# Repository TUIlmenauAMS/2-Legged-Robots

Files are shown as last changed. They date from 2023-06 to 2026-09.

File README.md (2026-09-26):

# 2-Legged-Robots

Program and 3D printing parts and description for little 2-legged robots, like in this picture,
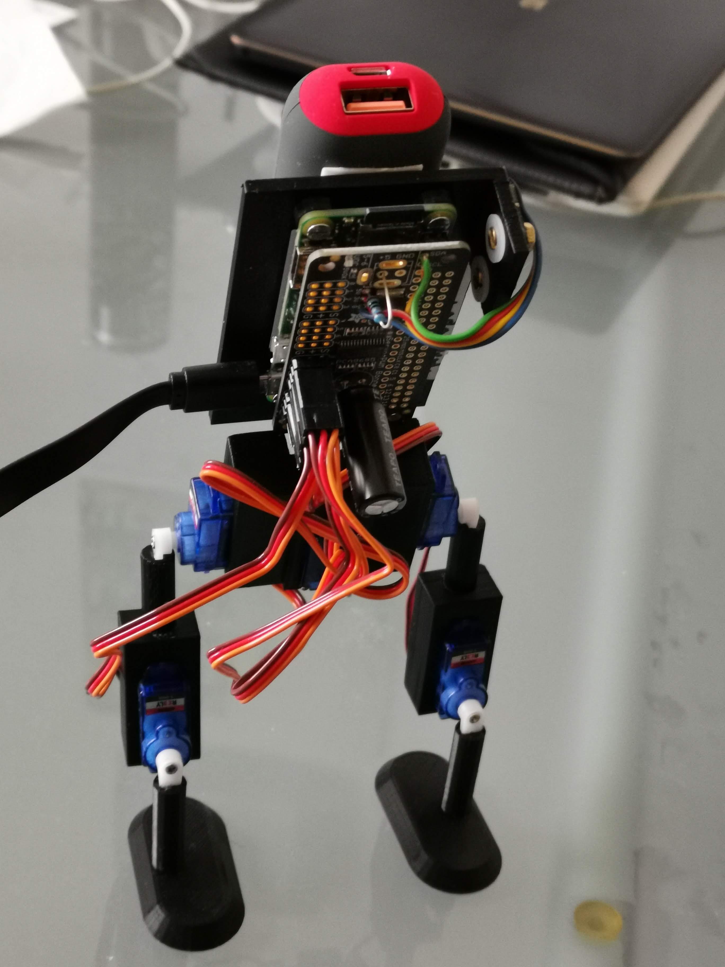
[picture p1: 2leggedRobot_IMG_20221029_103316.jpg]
.

Here is a video of the robot in action. There you can see the sideways spine joint and servo from behind (the white latch). This enables a simple and efficient way to shift the center of mass from one foot to the other, for walking:

https://player.vimeo.com/video/791830780?h=ef3d78c103

The "stl" parts are for my Raspirobo7 robot.
The "..bin.stl" files are binary stl files, which are needed for a MuJoCo simulation.
(Here is a partial simulation for back and hip: https://colab.research.google.com/drive/190HttyWH3-cmfSE2mszep3_cSGHyP7G-?usp=sharing)

Here is a complete simulation of the somewhat creative robot that was generated by Grok Build from this repository, which sill shows the resulting walking motion from the interplay of physics and the Python program, with a nice user interface for trying it out. You can also drag the view:

https://earth-drift-prairie-falcon.grok.me/

Building the robot needs:

- 2 foot_round075.stl

- 1 hueftservos.stl

- 2 knieservo_scad.stl

- 1 ruecken2.stl

Further parts:

- It is controlled by a Raspberry Pi Zero WH.

- Terratec P1 Powerbank Li-Ion 2600 mAh 171649, 5.49eur

- 5 servo motors REELY 36 ANALOG- SERVO 0008
(Nr. 1365555 / 4016138986273 or successor 2148502) at 4.99 eur (each)

- 3 AXIS DIGITAL ACCELERATION SENSOR MO, e.g. MMA8452Q
650514 / 4053199509867 , 6.99 eur.
Alternative MAKERFACTORY MF-6402108 accelerometer 
https://www.conrad.de/de/p/makerfactory-mf-6402108-beschleunigungssensor-1-st-2134036.html
7.49 eur.

- Elektrolytic-Capacitor 2200 uF, 16V,
Nr.: 1328835 - 62
Conrad Nr.: KSE228M016S1GBH25KFT, 0.20 eur

- 1 or 2 Ohm resistor 

- 4 wires, blue, yello, red, green.

- Ada3416  Adafruit 16-channel PWM/Servo.. 10.25
https://shop.pimoroni.com/products/adafruit-16-channel-pwm-servo-bonnet-for-raspberry-pi?variant=2821150736394 

- Micro SD Card, 32 GB, Noobs, 9.73 eur
https://shop.pimoroni.com/products/noobs-32gb-microsd-card-3-1?variant=31703694245971

The 2 ohm resistor is for the low pass filtered power suppy of the servo board. Since the servos can draw high power peaks, the 2200 uF capacitor is needed to supply thos power peaks. The resistor limits the current from the battery, to keep its volatge stable, to avoid the raspberry pi rebooting from a voltage drop. The 2 ohm resistor is solered in the servo board from the upper 5V soldering hole (viewed from looking at the front of the robot) to the left round soldering hole of the (unused) power plug. 

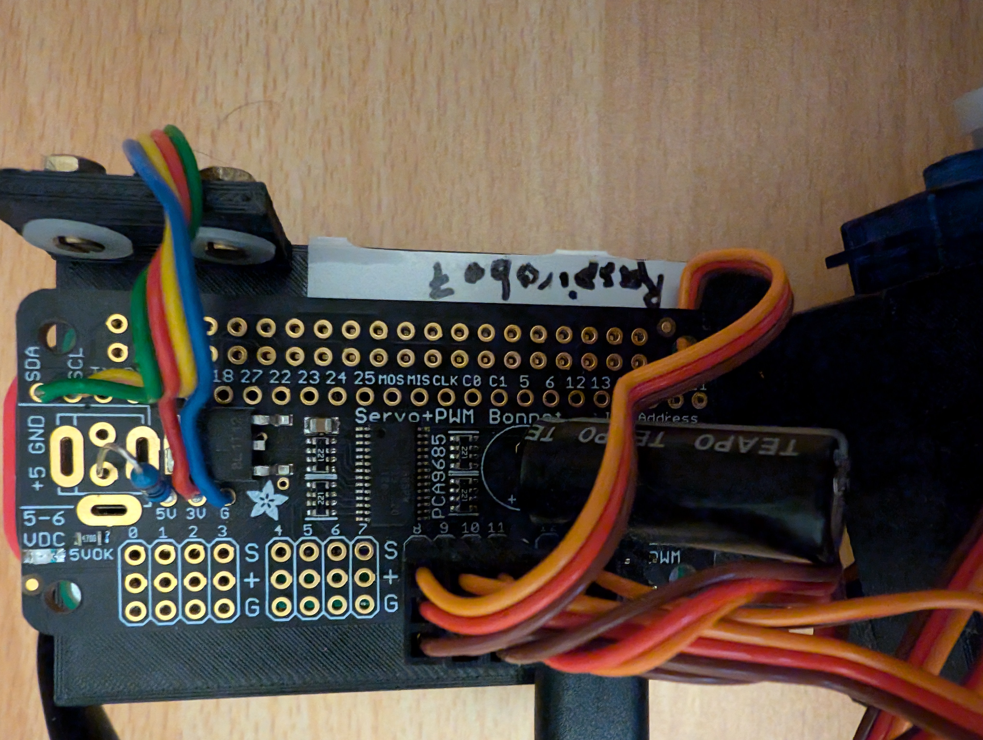
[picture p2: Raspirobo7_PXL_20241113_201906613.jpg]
This can be seen in this picture .

The acceleration sensor has the connections GND, scl, sda, 3V. They need to be connected, using flexible wires and soldering, to the corresponding soldering holes on the upper part ot the servo board.

As a first test after completing the hardware: after connecting with power, the LED's of both, the raspberry pi zero and also the servo shield, should light up. If not, the power is missing there.

The program "raspirobo7servoset90_only.py" sets all servos to the 90 degree position, for adjusting the legs and back to be straight at that position. This can also be used for testing the servos.

The program "raspirobo7servosetVertTilt.py" is for testing the accelerometer and find a vertical tilt angle that lets the robot stand in rest. This angel is then to be entered in the walking program "raspirobo7_balancing_learning2.py".

The program to let the robot walk in a learning manner is: "raspirobo7_balancing_learning2.py"

It uses our probabilistc optimization of "Random Directions" for learning and optimizing the walk. Hence it might take a while in the beginning until it learns to balance and walk.

Also see the information and videos on our Robotics website:

https://www.tu-ilmenau.de/en/university/departments/department-of-electrical-engineering-and-information-technology/profile/institutes-and-groups/applied-media-syste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

Many greetings,

  Gerald Schuller

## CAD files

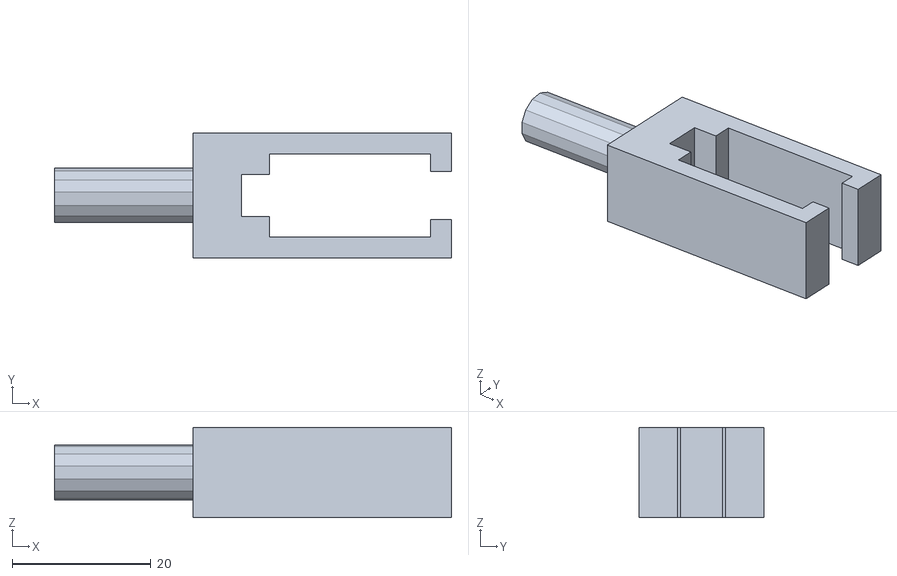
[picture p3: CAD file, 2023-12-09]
knieservo_scad-bin.stl
57.3 x 18.0 x 13.0

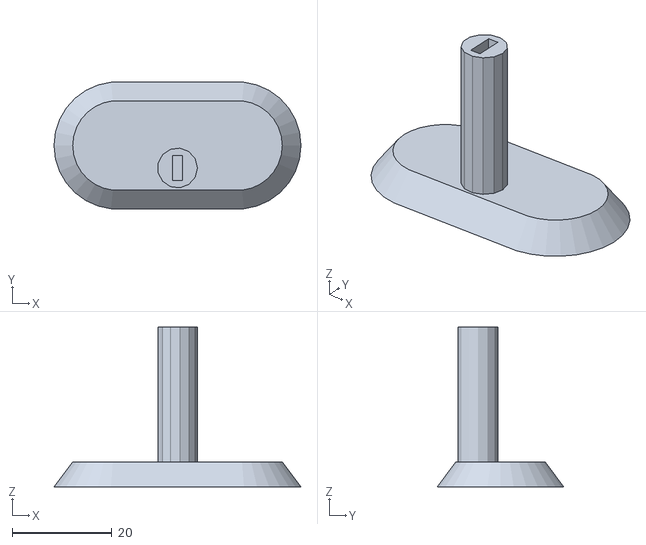
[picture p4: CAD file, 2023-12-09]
foot_round075-bin.stl
49.5 x 25.4 x 32.0

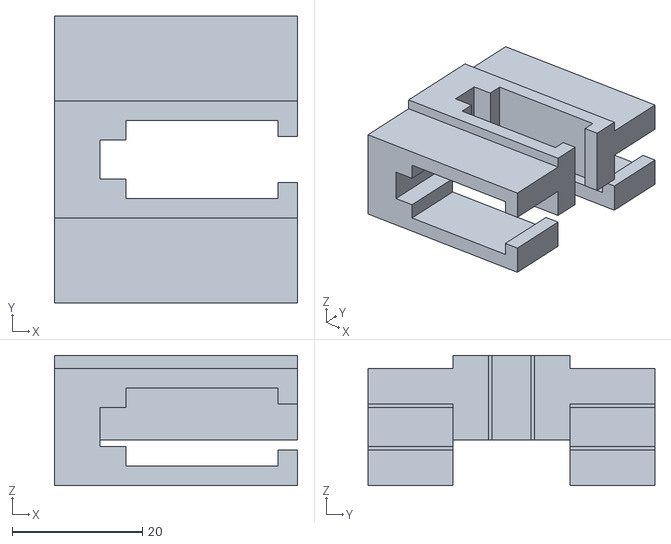
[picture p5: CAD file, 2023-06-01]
hueftservos_bin.stl
37.3 x 44.0 x 20.0

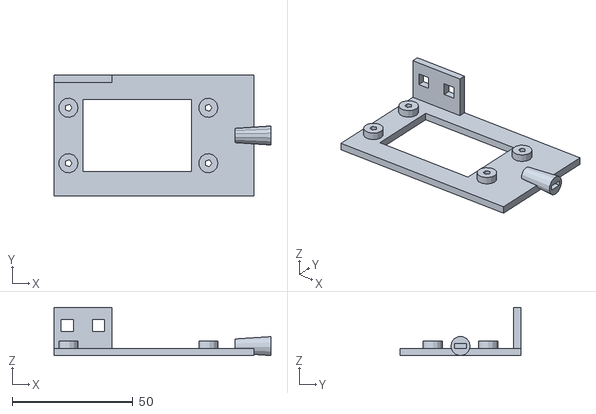
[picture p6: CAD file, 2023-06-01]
ruecken2bin.stl
90.0 x 50.0 x 20.0

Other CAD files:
hueftservos.stl
foot_round075.stl
ruecken2.stl
knieservo_scad.stl

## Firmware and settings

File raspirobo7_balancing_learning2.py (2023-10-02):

#Program to test the Raspirobo7 Robot with accelerometer and servo movement.
#For learning to balance itself using the random directions optimization.
#With side learning and storing of the optimized coefficients.
#Seems to be too wild after a while.
#Optimize for minimum variation for accelerometer measures despite disturbances from knee movements.
#Run it with:
#python3 raspirobo7_balancing_learning2.py
#
#You can check the I2C addresses of the devices connected to the Raspberry Pi using:
#sudo i2cdetect -y 1
#
#Includes a
#function to read accelerometer sensor MMA8452Q from the Raspberry Pi I2C port.
#See: http://ozzmaker.com/guide-to-interfacing-a-gyro-and-accelerometer-with-a-raspberry-pi/
#Based on:
#https://github.com/ControlEverythingCommunity/MMA8452Q/blob/master/Python/MMA8452Q.py
#Connections:
#http://www.pibits.net/code/mma8452q-accelerometer-and-raspberry-pi-example.php
#
#Data Sheet of MMA8452Q:
#https://www.robotshop.com/media/files/pdf/triple-axis-accelerometer-breakout-board-mma8452q-headers-datasheet.pdf
#Activate I2C bus on Raspi with "sudo raspi-config"
#Then:
#sudo apt-get install build-essential libi2c-dev i2c-tools python-dev libffi-dev
#sudo pip install cffi smbus2 (for python2, for python3 it should be smbus and pip3)
#sudo pip3 install adafruit-circuitpython-servokit
#name: raspirobo7
#Gerald Schuller, November 2022

#import smbus2 as smbus #for Python2
import smbus   #for Python3, install with pip
from lsm303d import LSM303D #install with pip
import time
import numpy as np
#from scipy.signal import medfilt
#import optimrandomdir as opt
import optimrandomdir_timevarying as opt

# Get I2C bus
bus = smbus.SMBus(1)
#For the servos:
from adafruit_servokit import ServoKit
lsm = LSM303D(0x1d)  # Change to 0x1e if you have soldered the address jumper


def readaccelerometer():
   #Read current accelerometer values
   #returns:
   #List of 3 float acceleration-values, [x,y,z]
   xyz = lsm.accelerometer()
   
   return xyz

#def balancing_obj(kcoeffs, tilts): #optimizing only side balance
#def balancing_obj(kfcoeffs, tilts): #optimizing only forward balance
def balancing_obj(coeffs, tilts):  #optimiizing both, side and forward balance
   #Objective function for balancing the robot such that the accelerometer is aligned to verttilt and hortilt, 
   #which are the sin of the angles to the vertical axis, vertical (front/back) and horizontally (left/right).
   #Arguments: kcoeffs: coefficients for the control lop
   #tilts: (verttilt, hortilt) target directions for balancing
   #Returns the error or objective function to minimize
   
   global YLP, YLPold, ydist, yold, Yvar, ZLP, ZLP1, ZLPold, ZLP1old, zdist, zold, Z, Zvar, phase, ampRH, ampLH;
   
   (verttilt, hortilt) = tilts  #hortilt is optimized
   kcoeffs=coeffs[0,:]
   kfcoeffs=coeffs[1,:]
   #hortilt=kcoeffs[3] #learned horizontal tilt
   #verttilt=kfcoeffs[3] #learned forward tilt
   
   for balancetrials in range(100): #Number of iterations for a set of control coefficients from optimizer, 
      #objective functions is returned at the end, to have a clearer picture if it is good.
      (X,Y,Z)=readaccelerometer()
      X=-X; Z=-Z #sign change for rotated accelerometer
      #print("(X,Y,Z)=", (X,Y,Z))
      #Y's:
      ydist+= (Y-verttilt)*(timestep);        #integral values (distance traveled, without artificial factor 100)
      ydist=np.clip(ydist,-0.1,0.1);
      YLPold=YLP
      YLP=0.99*YLP+0.01*Y
      yspeed=(Y-yold)/(timestep);  #differential values (speed, without artificial factor 100)
      ylpspeed=(YLP-YLPold)/(timestep)  #vert. speed from low passed version

      #Z's:
      """
      Zmem[0:(Lmed-1)]=Zmem[1:Lmed] #shift samples 
      Zmem[Lmed-1]=Z  #write latest sample, for median filter
      Z=medfilt(Zmem,kernel_size=Lmed)[int((Lmed-1)/2)]
      """
      
      zdist+= (Z-hortilt)*(timestep);
      zdist=np.clip(zdist,-0.1,0.1);

      #Sideways tilt:
      zspeed=(Z-zold)/(timestep);
      yold=Y;
      zold=Z;
      ZLPold=ZLP
      ZLP=0.99*ZLP+0.01*Z
      ZLP1old=ZLP1
      ZLP1=0.95*ZLP1+0.5*Z  
      zlpspeed=(ZLP-ZLPold)/(timestep)  #hor. speed from low passed version
      zlpspeed1=(ZLP1-ZLP1old)/(timestep) #hor. speed estimation from less low pass filtering
      
      #----------------------
      #PID control loop:
      #frontbalance = 180/3.14* 2.6*(ydist + 0.05*(Y-verttilt) -4*2.0e-2*ylpspeed) #2: schneller, without artificial factor 100
      #kf=np.array([1.3e+02, 6.3e+00, -1.2e+01, 5.6e-01]) #from learning robot 4, seems reasonably stable
      #kf=np.array([100, 100.0, -120])
      #kf=np.array([0, 6, 0])
      #kf=np.array([350, 20.0, -30])
      kf=kfcoeffs
      frontbalance = kf[0]*ydist + np.clip(kf[1]*(Y-verttilt),-10,10) + np.clip(kf[2]*ylpspeed,-10,10) 
      #sidebalance = -180/3.14* 2.9*(zdist + 0.05*(Z-hortilt) -2*4.0e-2*zlpspeed)*1.0;# k2=4e-4 #2: schneller, without artificial factor 100. k1 needs to be larger for faster steps, ca. 0.7 fuer speed 0.25. k2 was originally with - sign, but with plus seems to be better!
      #k=np.array([-3.2e+02, -1.5e+01, 3.4e+00, 1.4e-01]) #This set makes it oscillate! From learning robot4
      #Manual tuning of the PID controller: https://en.wikipedia.org/wiki/PID_controller
      #Increase each coeff until oscillation, then half it, first propoertional, then integral, then differential. 
      #k=np.array([-200, -1.5e+01, 28])
      #k=np.array([-350, -20.0, 30])
      #k=np.array([-1000, -1000.0, 1200]) #P: 30 makes it oscillate, so half: 15, I: 400 oscillates, so half, 200
      #k=np.array([-1000, -100.0, 10])
      #k=np.array([-1000, -100.0, 400])
      k=kcoeffs; #Read control coefficients from function argument
      #k=np.array([ 10.89118321,   4.93782397, -10.27297858,   3.8025568 ]); hortilt=k[3] #optimized with step excitation
      #k=np.array([ 10.89118321,   4.93782397, -10.27297858,   -0.15 ]); hortilt=k[3] #optimized with step excitation, k[3] needs to be manually tuned for back upright, more negative values tilt more left, as seen from the Robot. -0.3, -0.15. But attention: Changes because it is part of the optimization, which makes the robot sometimes turn or go in circles. So it could also be left at 0.0. Not really, kcoeffs is not used, only the preset above!
      sidebalance = k[0]*zdist + np.clip(k[1]*(Z-hortilt), -10, 10) + np.clip(k[2]*zlpspeed, -10,10) #+ np.clip(k[3]*zlpspeed1, -10,10)
      sidebalance=np.clip(sidebalance,-50,50);
      #print("sidebalance=", sidebalance)
      #print("k[0]*zdist=", k[0]*zdist, "k[1]*(Z-hortilt)=", k[1]*(Z-hortilt), "k[2]*zlpspeed=", k[2]*zlpspeed, "Z=", Z)
      #----------------------------
      #Servo control:
      angle=-frontbalance+110+1*ampRH; #sign change because of flipping hip servos, with tuning offsets. The number (110) needs to be manually tune for the legs being parallel in the beginning.
      huefterechts.angle=np.clip(int(angle + huefterechts_offset),0, 180); 
      angle=frontbalance+90+1*ampLH; #sign change because of flipping hip servos
      hueftelinks.angle=np.clip(int(angle + hueftelinks_offset),0,180); 
      #print("ampRK=", ampRK, "ampLK=", ampLK)
      
      #Independent Knee movements:
      #"""
      angle=0.4*sidebalance+knierechtsbalance+90-0-ampRK + knierechts_offset; #0.5
      knierechts.angle=np.clip(int(angle),0,180);
      #print("r=",np.clip(int(angle),0,180))
      angle=0.4*sidebalance+knielinksbalance+90+0-ampLK + knielinks_offset; #0.5
      knielinks.angle=np.clip(int(angle),0,180); 
      #print("l=",np.clip(int(angle),0,180))
      #"""
      
      #horangle=np.arcsin(hortilt)/3.14*180 #convert from radians to degrees
      #spine.angle = np.clip(int(90 + spine_offset - 0.0*horangle),0,180);
      #spine.angle = np.clip(int(90 + 0.6*sidebalance),0,180);
      spine.angle = np.clip(int(90 + 4.0*sidebalance),45,135); #2.0
      #spine.angle = 90 + spine_offset + hortiltdeg;
      #print("int(90 + spine_offset )=", int(90 + spine_offset ))
      #print("horangle=", horangle)
      #print("0.5*sidebalance=", 0.5*sidebalance)
      
      #Perturbation:
      #Move knees:
      """
      ctr+=1
      if ctr%50==0: #every second change horizontal tilt for control loop testing:
         hortiltoffset=-hortiltoffset
         #Perturbation at knees: Doesn't reall work because the balancing function overwrites it! Turned off the knee control
         angleknee=(np.random.rand()-0.5)*20 #+-5 Grad
         angleknee = -angleknee #flip direction
      """
      #Knee moves:
      """ 
      angleknee =-amptilt*np.sign(np.cos(phase))*(abs(np.cos(phase))**(0.5))
      #angleknee=(np.random.rand()-0.5)*20 #+-10 Grad
      #print("angleknee=", angleknee)
      knierechts.angle=90.0 + knierechts_offset+angleknee 
      knielinks.angle=90.0 + knielinks_offset + angleknee
      #walking movement back-forth:
      ampLH=-3.0*(np.sin(phase))
      ampRH=-3.0*(np.sin(phase))
      """
      #"""
      #Steps according to tilt:
      #hortiltoffset=-amptilt*np.cos(phase) #amptilt=-0.2,-0.08
      #angleknee=(np.random.rand()-0.5)*2 #+-1 Grad random excitation
      ampLH += np.sign(Z -hortiltadj)*5 #stepincrement
      ampLH= np.clip(ampLH, -5, 5)
      ampRH += np.sign(Z -hortiltadj)*5
      ampRH = np.clip(ampRH, -5, 5)
      #"""
      Yvar= 0.99*Yvar+0.01*((Y-YLP)**2)
      Zvar= 0.99*Zvar+0.01*((Z-ZLP)**2)
      phase+=speed
      time.sleep(timestep)
   print("Zvar=", Zvar, "Yvar=", Yvar, "Y=", Y)
   #print("kfcoeffs=", kfcoeffs)
   #print("fcoeffs=", coeffs)
   #return Zvar +Yvar
   #return Yvar
   #return Zvar
   return abs(Zvar-0.1) #0.06, 0.1, 0.15

#--------------------------------------------------------------


#Testing:
if __name__ == '__main__':
   
   #Initializations:
   # Set channels to the number of servo channels on your kit.
   # 8 for FeatherWing, 16 for Shield/HAT/Bonnet.
   kit = ServoKit(channels=16)
   
   Lmed=3 #should be odd
   phase=0.0

   schrittzaehler=0
   ampRK=0 #right knee step
   ampLK=0 #Left knee step
   huefterechts=kit.servo[8]
   hueftelinks=kit.servo[9]
   knierechts=kit.servo[10]
   knielinks=kit.servo[11]
   spine=kit.servo[12]
         
   """
   for s in range(16):
      #test if accelerometer works, move accelerometer, the printed values should change:
      (X,Y,Z)=readaccelerometer()
      #print("Accelerometer X,Y,Z=", round(X,2),round(Y,2),round(Z,2))  
      
      #makes servos go first to positive, then to negative direction, relative to 90 degrees,
      #servos connected to connector 0 to 15, 1 period for each:
      print("Servo:", s)
      kit.servo[s].angle = 90 
   """
   #tune to balance upright:
   verttiltdeg = 32 #tilt forward in degrees
   hortiltdeg = 0 #5, +/- 10 for balancing on one foot, tilt left in degrees (right tilt: negative), should be balanced with this
   verttilt= np.sin(verttiltdeg/180*3.14) #0.5
   hortiltadj= np.sin(hortiltdeg/180*3.14) #adjusted horizontal tilt, from balancing in rest
   
   hueftelinks_offset= -(verttiltdeg) #+60 tilt forward, negative: move leg backward, negative sign because robo7 has turned around hip servos
   huefterechts_offset= -( -verttiltdeg) #-60 tilt forward, negative: move leg forward, negative sign because robo7 has turned around hip servos
   knielinks_offset= 5.0  + hortiltdeg #-1 spread lower legs, positive: move leg left (seen from the robot)
   knierechts_offset= 0.0  + hortiltdeg  #+1 #spread lower legs, tilt right, negative: move leg right
   #spine_offset = 0  #offset for the spine servo, negative: to the right (seen from robot), should be straight up (accelerometer data=0) for hortiltdeg=0 and straight legs
   


   
   ampRH=0.0;ampLH=0.0; ampLK=0.0; ampRK=0.0 #amplitudes for the steps
   knierechtsbalance=0.0
   knielinksbalance=0.0
   #Global low pass filter variables for the balancing control loop:
   ydist=0
   yold=0
   zdist=0.0;
   zold=0.0
   ZLP=0.0
   ZLPold=0.0
   ZLP1=0.0 #for less low pass filtering of Z
   ZLP1old=0.0
   YLP=0.0
   YLPold=0.0
   Yvar=0.0; Zvar=0;
   Zmem=np.zeros(Lmed) #For median filter of length Lmed
   Z=0;
   
   timestep=0.01 #time step in seconds, larger for optimization?
   hortiltoffset=0.0 #Horizontal tilt variable for walking
   #hortiltoffset=0
   ctr=0
   angleknee=6 #degrees
   phase=0;
   amptilt=8 #6 #amplitude of knees in degrees
   speed=0.1;  #phase increment in radiants for servo, speed is forward
   
   """
   #setting before control loop not really necessary:
   huefterechts.angle=100.0 + huefterechts_offset #-60 #tilt forward
   hueftelinks.angle=90.0 + hueftelinks_offset #+60
   angleknee=0
   knierechts.angle=90.0 + knierechts_offset+angleknee #+1 #spread lower legs
   knielinks.angle=90.0 + knielinks_offset + angleknee #-1
   spine.angle= 90 + hortiltdeg#
   """
   
   #initx=np.array([-350, -20.0, 30])
   #initx=(np.random.rand(4)-0.5) #optimizing only side balance
   """
   try:
      #use loadtxt instead of pickle for easier editing:
      print("Load robocoeffs7.txt")
      initx= np.loadtxt("/home/schuller/Robots/robocoeffs7.txt")
   except IOError:
      print("robocoeff.pickle file not found, fresh start")
      #k=np.array([-166.2, -8.31, -0.066, 0.1])
      initx=(np.random.rand(2,4)-0.5) #optimizing both side and forward balance, and hor tilt
   """
   initx=(np.random.rand(2,4)-0.5) #optimizing both side and forward balance, and hor tilt
   args=(verttilt , hortiltadj+hortiltoffset)
   xmin= opt.optimrandomdir(balancing_obj, initx, args=args, iterations=100, startingscale=1.0, endscale=0.0) #100 iterations should be about 100 seconds.
   
   #use savetxt instead of pickle for easier editing:
   """
   os.system('cp -p robocoeffs7.txt robocoeffs7_o.txt') #backup in case of losses
   np.savetxt("robocoeffs7.txt", xmin)
   print("Wrote k and kf to file robocoeffs7.txt")
   """

   """
   while True:
      tilts=(verttilt , hortiltadj+hortiltoffset)
      kcoeffs=np.array([-350, -20.0, 30])
      balancing_obj(kcoeffs, tilts)
      
      #print("next setp")
      
      phase+=speed
      #time.sleep(timestep)
   """
      

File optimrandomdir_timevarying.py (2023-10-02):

#Program for optimizing (minimizing) using our algorithm of "random directions".
#usage: coeffmin=optimrandomdir(objfunction, coeffs, args=(X,))
#arguments: objfunction: name of objective function to minimize
#coeffs: Starting vector for the optimization, also determines the dimensionality of the input for objfunction
#Can be a tensor of any dimension!
#X: further arguments for objfunction
#With line search for successful directions
#For time varying objective functions, hence x0 is computed every time in the beginning of the optimizazion loop.
#returns: coeffmin: coeff vector which minimizes objfunction
#Gerald Schuller, August 2021

import numpy as np

def objfunccomp(objfunction, coeffs, args, bounds):
   #compact objective function for optimization
   if bounds !=():
         for n in range(len(bounds)):
            coeffs[n]=np.clip(coeffs[n],bounds[n][0], bounds[n][1])
   if len(args)==0:
      X0=objfunction(coeffs)
   elif len(args)==1:
      X0=objfunction(coeffs, args[0])
   else:
      X0=objfunction(coeffs, args)
   return X0
   

def optimrandomdir(objfunction, coeffs, args=(), bounds=(), coeffdeviation=1.0, iterations=1000, startingscale=2, endscale=0.0):
   #Reads in a block of a stereo signal, improves the unmixing coefficients,
   #applies them and returns the unmixed block
   #Arguments: objfunction: (char string) name of objective function to minimize
   #coeffs: array of the coefficients for which to optimize
   #args: Additional arguments for objfunction, must be a tuple! (in round parenthesis)
   #bounds: bounds for variables or coefficients, sequence (Tuple or list) of pairs of minima and maxima for each coefficient (optional)
   #This sequence can be shorter than the coefficent array, then it is only applied to the first coefficients that the bounds cover.
   #This can be used to include side conditions. Example: bounds=((0,1.5),(-1.57,1.57))
   #coeffdeviation: array of the expected standard deviation of the coefficients
   #iterations: number of iterations for optimization
   #startingscale: scale for the standard deviation for the random numbers at the beginning of the iterations 
   #endscale: scale of the random numbers et the end of the iterations.
   #returns: 
   #Xunm: the unmixed stereo block resulting from the updated coefficients 
   #coeffsmin: The coefficients which minimize objfunction
   
   
   #print("args=", args, "args[0]=", args[0])
   coeffs=np.array(coeffs) #turn into numpy array (if not already)
   sh=coeffs.shape #shape of objfunction input
   #Simple online optimization, using random directions optimization:
   #Initialization of the deviation vector:
   #print("coeffdeviation=", coeffdeviation)

   try:
      if coeffdeviation==1.0:
         coeffdeviation=np.ones(sh)*1.0
   except:
      print("use specified coefficient std. deviations")


   """
   if len(args)==0:
      X0=objfunction(coeffs)
   elif len(args)==1:
      X0=objfunction(coeffs, args[0])
   else:
      X0=objfunction(coeffs, args)
   """
   """
   argstr=''
   for i in range(len(args)):
      argstr+=',args['+str(i)+']'
   argstr=argstr[1:]
   print('argstr=', argstr)
   print("eval(argstr)=", eval(argstr))
   #print("Call=", objfunction+'(coeffs'+argstr+')')
   #X0=eval(objfunction+'(coeffs'+argstr+')')
   #X0=objfunction(coeffs, eval(argstr))
   X0=objfunction(coeffs, args)
   """
   
   #Small random variation of coefficients, -0.05..0.05 for attenuations, -0.5..0.5 for delays:
   #coeffdeviation=np.array([0.1,0.1,1.0,1.0])*0.8
   #setfrac=8/max(sh) #0.0 <= setfrac <=1.0, 
               #probability of a coefficent to be updated, for reducing dimensionality. 
               #1.0: all coeffs are updated
               #A simple way to create subspaces of lower dimensionality
               #if setfrac is too small it easily gets stuck in local minima.
   #print("sh*2=", sh*2)
   #subspacematrix=np.random.normal(loc=0.0, scale=1.0, size=sh*2) #random matrix of size sh x sh, subspace approach
   m=0; mlastupdate=0
   #iterations=300  #for the optimization, 100000 for LDFB, set below as global variable
   #scale=1.0  #standard deviation for the gaussian random number generator
   scalehistsize=10
   scalehistory=np.zeros((scalehistsize,2))
   alpha=1/(2*len(coeffs)) #update factor for scale
   #alpha=1/(2*8)
   succ=False
   mean=np.zeros(sh)
   for m in range(iterations):
   #while (np.linalg.norm(coeffdeviation)>1e-6):
      #Old values 0, starting point:
      X0=objfunccomp(objfunction, coeffs, args, bounds)
      setfrac=4/max(sh) #take subspace of about 8 or 4 coefficients
      #setfrac=max(8.0/max(sh),8.0/iterations) #take larger subspaces such that larger dimensions can be fully covered more easily
      #setfrac=np.random.rand(1) #random fraction of coefficients
      #scale=np.random.rand(1); #random scale (std. deviation for gauss distribution)
      #setfrac=np.clip(1.0-m/iterations,1/sh[0],1) #begin with global optimization, later fine tune coeff in lower dimensions
      #setfrac=np.clip(1.0-m/iterations,np.sqrt(8.0/max(sh)),1)**2 #begin with global optimization, later fine tune coeff in lower dimensions
      #setfrac=np.clip(1.0-m/iterations,8.0/max(sh),1) #begin with global optimization, later fine tune coeff in lower dimensions
      #setfrac=np.clip(m/iterations,1/sh[0],1) #begin with small dimension, later fine tune coeff in higher dimensions
      #setfrac=setfrac **2 #become smaller faster
      #setfrac=setfrac ** 0.5 #become faster slower
      #scale=abs(np.random.normal(loc=0.0, scale=1.0, size=1)[0])
      #scale=np.random.rand(1)[0]
      #scale=((1.0-m/iterations))
      #scale=(1.4*(1.0-m/iterations))**2
      scale=np.clip((startingscale-endscale)*((1.0-1.0*m/iterations)**2)+endscale,1e-4,None)  #scale becomes smaller when iterations icrease (so far best)
      #scale=np.clip((startingscale-endscale)*(np.sin(6.28/iterations*10*m)**2)+endscale,1e-4,None)  #scale oscillates with iterations 
      #scale=4.0*np.exp(-8*m/iterations)
      #scale*=0.9999  #exponential decay of scale of random numbers
      if m%1000==0:
         print("m=", m, "setfrac=", setfrac, "scale=", scale ); m+=1
      #print("sh*2=", sh*2)
      #coeffvariation=(np.random.rand(4)-0.5)*coeffdeviation
      #coeffvariation=4*(np.random.random(sh)-0.5)*coeffdeviation  #small variation, uniform distribution
      #coeffset=np.ones(coeffs.shape)
      coeffset=np.random.random(coeffs.shape)<=setfrac #Set of coefficients to be updated
      #print("coeffdeviation=", coeffdeviation)
      #if succ==False:
      coeffvariation=np.random.normal(loc=mean, scale=scale*coeffdeviation) #Gaussian distribution
      coeffvariation *= coeffset #keep only the variation in the subset, for sparse coefficients
      #coeffvariation=np.dot(subspacematrix,coeffvariation)  #subspace approach
      #print("coeffvariation=", coeffvariation)
      #new values 1:
      """
      if args==():
         X1=eval(objfunction+'(coeffs+coeffvariation)')
      else:
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
